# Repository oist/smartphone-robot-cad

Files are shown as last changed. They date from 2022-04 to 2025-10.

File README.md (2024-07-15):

# CAD for the OIST smartphone robots

This repository contains the CAD files for the OIST smartphone robots.

- [./body](./body) contains standard 3D CAD files used for the robot's 3D printed body.
- [./pcb](./pcb) contains the KiCad files for the robot's PCB and schematic design.

These two subprojects (body and pcb) have direct dependencies on each other as the 3D CAD design is based on the PCB design.
It is likely a good idea to manage the development of each on a separate branch and merge them together when necessary.

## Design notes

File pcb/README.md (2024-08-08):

# Smartphone Robot PCB and Schematic Design
The schematic and PCB design for the smartphone robot was done in KiCAD.

The most recent version was created in Kicad v7 so be sure to use that when opening the project else you may run into compatibility issues.

# Cloning the Repo
Currently this repo is an OIST internal repo, so read access is only given to specific users. Add external users for collaboration.

Note this repo uses a central library management system. Symbols, footprints, and models are maintained on a personal fork of the central kicad library repos. These forks are maintained as submodules within the kicad-symbols, kicad-footprints, and kicad-packages3D respectively under:

[https://github.com/oist/smartphone-robot-cad/tree/main/kicad/](https://github.com/oist/smartphone-robot-cad/tree/main/kicad/)

Those forks should all be public and you should be able to clone the main repo with submodules without additional access, but just in case, here are the links to the forks:
- [https://gitlab.com/topherbuckley/kicad-symbols](https://gitlab.com/topherbuckley/kicad-symbols)
- [https://gitlab.com/topherbuckley/kicad-footprints](https://gitlab.com/topherbuckley/kicad-footprints)
- [https://gitlab.com/topherbuckley/kicad-packages3D](https://gitlab.com/topherbuckley/kicad-packages3D)

The easiest way to clone including all submodules would likely be `git clone --recurse-submodules -j8 git@github.com:oist/smartphone-robot-cad.git' if you are having trouble with that, you can refer to these links for details:

- [StackOverflow](https://stackoverflow.com/questions/3796927/how-do-i-git-clone-a-repo-including-its-submodules)
- [Git Docs](https://git-scm.com/docs/git-submodule)

Note that because of the main repo and submodules are hosted on two different platforms (github and gitlab) you must have credentials for both platforms. You can use your github credentials to setup a gitlab account and add your existing SSH keys to your gitlab account. More on how to do that [here](https://docs.gitlab.com/ee/user/ssh.html)

# Setting up the Environment

KiCAD makes use of user configuration files to define libraries, so without modifying your setup, you will unlikely be able to resolve the majority of libraries used in this project. There are many ways to go about this, of which you can find more details in the links below:

- [Project Collaboration Tips](https://forum.kicad.info/t/project-and-libary-setup-for-sharing-and-collaboration-kicad-version-5/20842/2) (See section Simplify First Time Setup...)

This repo has been set up to make using environmental variables the easiest option. In the `config` directory you will find a subdirectories corresponding to minor version of KiCAD. If you add an environment variable for KICAD_CONFIG_HOME pointing to this `config` directory, KiCAD will use these configuration files rather than the defaults. On Ubuntu 20.04 the default is `~/.config/kicad/`. Note you must then open kicad from a terminal that as properly sourced the newly created environmental variables. In a bash terminal this would be:

```
source KICAD_CONFIG_HOME=[path_to_repo]/config
kicad
```

Note this will use blank (default or empty)  configurations, so feel free to copy/paste your personal configurations into this `config` directory as all files other than `sym-lib-table` and `fp-lib-table` are ignored by the `.gitignore` file.

# LED Inidications
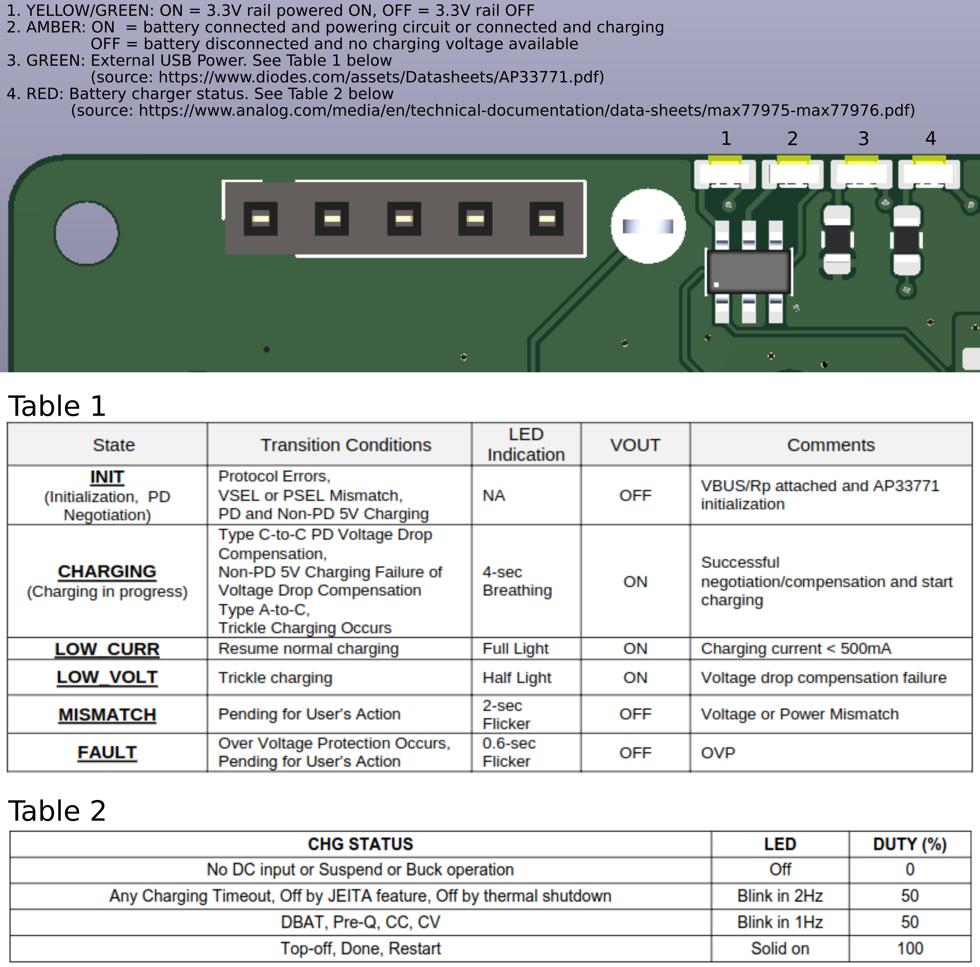
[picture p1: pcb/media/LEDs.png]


# Additional References
- [Good discussion on KiCAD Collaboration and Versioning](https://forum.kicad.info/t/working-collaborately-on-projects-using-git/16114/11)
- [Nice tools for versioning](https://jnavila.github.io/plotkicadsch/)

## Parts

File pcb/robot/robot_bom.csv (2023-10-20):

Manufacturer | Part Number | Ref | Qty Single Board | Description | Batch Size | Qty Total Batch | Customer Stock | Value | Footprint
Murata | GRM188R61A226ME15D | C1,C33,C34,C76,C78,C87,C93 | 7 | Unpolarized capacitor | 5 | 35 | 0 | 22uF | robot:C_0603_1608Metric
Murata | GRM1555C1H270JA01J | C2,C3,C18,C19,C45,C46 | 6 | Unpolarized capacitor | 5 | 30 | 0 | 27pF | robot:C_0402_1005Metric
Murata | GRM155R61E105KA12D | C4,C8,C10,C21,C22,C29,C47,C48,C50,C51,C52,C53,C54,C55,C69,C88,C94,C95,C105,C126 | 20 | Unpolarized capacitor | 5 | 100 | 10 | 1uF | robot:C_0402_1005Metric
Murata | GRM155R62A104KE14D | C5,C6,C7,C9,C11,C12,C13,C14,C15,C16,C24,C32,C35,C36,C37,C38,C39,C40,C41,C44,C57,C58,C59,C60,C61,C62,C63,C64,C65,C66,C70,C71,C72,C73,C85,C92,C102,C103,C104,C113,C114,C116,C119,C121 | 44 | Unpolarized capacitor | 5 | 220 | 0 | 0.1uF | robot:C_0402_1005Metric
Murata | GRM188R61E106KA73J | C17,C20,C25,C27,C42,C43,C67,C68,C75,C77,C80,C129,C130,C132,C134,C136 | 16 | Unpolarized capacitor | 5 | 80 | 0 | 10uF | robot:C_0603_1608Metric
Murata | GRM188R61E475KE11D | C23,C97,C100,C101,C124 | 5 | Unpolarized capacitor | 5 | 25 | 0 | 4.7uF | robot:C_0603_1608Metric
Samsung | CL10B474KO8NNNC | C26,C56 | 2 | Unpolarized capacitor | 5 | 10 | 0 | 0.47uF | robot:C_0603_1608Metric
Samsung | CL10A225KP8NNNC | C28,C49 | 2 | Unpolarized capacitor | 5 | 10 | 0 | 2.2uF | robot:C_0603_1608Metric
Samsung | CL10B224KA8NNNC | C30,C31 | 2 | Unpolarized capacitor | 5 | 10 | 0 | 0.22uF | robot:C_0603_1608Metric
Samsung Electro-Mechanics | CL21A476MRYNNNE | C81 | 1 | Unpolarized capacitor | 5 | 5 | 0 | 47uF | robot:C_0805_2012Metric
Murata | GRM31CD80J107MEA8K | C82,C83,C109,C125,C127 | 5 | Unpolarized capacitor | 5 | 25 | 20 | 100uF | robot:C_1206_3216Metric
Würth Elektronik | 885012205067 | C84,C115,C118 | 3 | Unpolarized capacitor | 5 | 15 | 0 | 10nF | robot:C_0402_1005Metric
Murata | GRM155R71H223KA12J | C110,C117,C120 | 3 | Unpolarized capacitor | 5 | 15 | 0 | 22nF | robot:C_0402_1005Metric
Murata | GCM155R71H152KA37D | C111 | 1 | Unpolarized capacitor | 5 | 5 | 0 | 1.5nF | robot:C_0402_1005Metric
Murata | GCM155R71H332KA37J | C112,C122 | 2 | Unpolarized capacitor | 5 | 10 | 0 | 3.3nF | robot:C_0402_1005Metric
Murata | GRM155R71H473KE14D | C123,C128 | 2 | Unpolarized capacitor | 5 | 10 | 0 | 47nF | robot:C_0402_1005Metric
Cal-Chip Electronics, Inc. | GMC32X5R107M16NT | C131,C137 | 2 | Unpolarized capacitor | 5 | 10 | 0 | 100uF | robot:C_1210_3225Metric
Harvatek Corporation | B12H1USD-20D000234U1930 | D1 | 1 | Light emitting diode | 5 | 5 | 0 | LED-RED | robot:B12H1UYG-20D000134U1930
Harvatek Corporation | B12H1UYG-20D000134U1930 | D2 | 1 | Light emitting diode | 5 | 5 | 0 | LED-YG | robot:B12H1UYG-20D000134U1930
Harvatek Corporation | B12H1UY--20D000134U1930 | D3 | 1 | Light emitting diode | 5 | 5 | 0 | LED-Amber | robot:B12H1UYG-20D000134U1930
Littelfuse Inc. | SMF13A | D4,D6,D10 | 3 | Zener diode | 5 | 15 | 0 | SMF13A | robot:D_SOD-123F
Harvatek Corporation | B12H1NG--20D000134U1930 | D5 | 1 | Light emitting diode | 5 | 5 | 0 | LED-GREEN | robot:B12H1UYG-20D000134U1930
KYOCERA AVX | SD2114S040S8R0 | D7 | 1 |  | 5 | 5 | 0 | D_Schottky | robot:SD2114S040S8R0
Diodes Incorporated | 1N4448HLP-7 | D9,D11 | 2 | Diode | 5 | 10 | 0 | IN4448HLP | robot:D_0402_1005Metric
Texas Instruments | TPS22998RYZR | IC1 | 1 | Power Switch ICs - Power Distribution | 5 | 5 | 0 | TPS22998RYZR | robot:TPS22998RYZR
Amphenol Commercial Products | 12401610E4#2A | J1 | 1 |  | 5 | 5 | 0 | USBC_Receptacle_SMD_RA | robot:CON_USB3.1-C_RCPT_SMD_RA_ACP_12401610E4#2A
Adam Tech | PH1-05-UA | J2 | 1 | Generic connector, single row, 01x05, script generated (kicad-library-utils/schlib/autogen/connector/) | 5 | 5 | 0 | Conn_01x05 | robot:PinSocket_1x05_P2.54mm_Vertical
JST | B6B-ZR-SM4-TF | J3,J5 | 2 | Generic connectable mounting pin connector, single row, 01x06, script generated (kicad-library-utils/schlib/autogen/connector/) | 5 | 10 | 0 | Conn_01x06_MountingPin | robot:CONN_B6B-ZR-SM4-TF_JST
GCT | USB4151-GF-C | J4 | 1 |  | 5 | 5 | 0 | USB4151-GF-C | robot:GCT_USB4151-GF-C_REVA
TAIYO YUDEN | NRS6028T1R5NMGJ | L1,L3 | 2 | Inductor | 5 | 10 | 0 | 1.5uH | robot:NRS6028T1R5NMGJ
Vishay | IHLP2020BZERR47M01 | L2,L4 | 2 | Inductor symbol for simulation only | 5 | 10 | 0 | 0.47uH | robot:Vishay-IHLP-2020BZ-FP_1.905x2.79-3D_2.0-0-0-MFG
ANBON SEMICONDUCTOR (INT'L) LIMITED | BSS138 | Q1,Q7 | 2 | N-MOSFET transistor, gate/source/drain | 5 | 10 | 0 | Q_NMOS_GDS | robot:SOT-23
ON Semiconductor | EFC8811R-TF | Q2 | 1 | EFC8811R-TF | 5 | 5 | 19 | EFC8811R-TF | robot:ON_Semiconductor-568AL-10_2013-O-MFG
ANBON SEMICONDUCTOR (INT'L) LIMITED | AS2312 | Q3 | 1 | 20V Vds, 0.63 Id, N-Channel MOSFET with ESD protection, SOT-523 | 5 | 5 | 0 | AS2312 | robot:SOT-23
Yangjie Electronic Technology | YJL3416A | Q4 | 1 | 20V Vds, 0.63 Id, N-Channel MOSFET with ESD protection, SOT-523 | 5 | 5 | 0 | YJL3416A | robot:SOT-23
Texas Instruments | SN74AHC125RGYR | Q5,Q6 | 2 | Buffer/Line Driver 4-CH Non-Inverting 3-ST CMOS 14-Pin VQFN EP T/R | 5 | 10 | 39 | SN74AHC125RGYR | robot:SN74AHC125RGYR
Walsin Technologies | WR04X102 JTL | R1,R5,R46,R47,R50 | 5 | Resistor | 5 | 25 | 0 | 1k | robot:R_0402_1005Metric
Stackpole Electronics | RMCF0402JT27R0 | R3,R4 | 2 | Resistor | 5 | 10 | 0 | 27 | robot:R_0402_1005Metric
Yageo | RC0402FR-1310RL | R6,R7,R32,R33,R41,R42 | 6 | Resistor | 5 | 30 | 0 | 10 | robot:R_0402_1005Metric
Stackpole Electronics | RMCF0603JT47K0 | R8,R18 | 2 | Resistor | 5 | 10 | 0 | 47K | robot:R_0603_1608Metric
Stackpole Electronics | RMCF0402FT80K6 | R9 | 1 | Resistor | 5 | 5 | 0 | 80.6k | robot:R_0402_1005Metric
Stackpole Electronics | RMCF0805ZT0R00 | R11,R52,R54,R67,R68,R69,R70,R71,R72,R73,R74,R77,R78 | 13 | Resistor | 5 | 65 | 0 | 0 | robot:R_0805_2012Metric
Walsin Technology | WR06X1003FTL | R12,R17,R49,R59,R60,R61,R89,R99 | 8 | Resistor | 5 | 40 | 0 | 100k | robot:R_0603_1608Metric
Stackpole Electronics | RMCF0603JT2K20 | R14,R15,R20,R21,R34,R35 | 6 | Resistor | 5 | 30 | 0 | 2.2k | robot:R_0603_1608Metric
Stackpole Electronics | RMCF0603JT510K | R16 | 1 | Resistor | 5 | 5 | 0 | 510k | robot:R_0603_1608Metric
Stackpole Electronics | RMCF0603JT200K | R19,R36 | 2 | Resistor | 5 | 10 | 0 | 200k | robot:R_0603_1608Metric
Stackpole Electronics | RMCF0603JT100R | R22,R23,R24,R25,R56,R58,R97 | 7 | Resistor | 5 | 35 | 0 | 100 | robot:R_0603_1608Metric
Walsin Technology | WR06X1002FTL | R28,R31,R96,R102 | 4 | Resistor | 5 | 20 | 0 | 10k | robot:R_0603_1608Metric
Panasonic | ERJ-3RQJR39V | R29,R30 | 2 | Resistor | 5 | 10 | 10 | 0.39 | robot:R_0603_1608Metric
Panasonic | ERJ-3EKF6493V | R37,R39 | 2 | Resistor | 5 | 10 | 0 | 649k | robot:R_0603_1608Metric
Stackpole Electronics | RMCF0603JT120K | R38,R40 | 2 | Resistor | 5 | 10 | 0 | 120k | robot:R_0603_1608Metric
Panasonic | ERJ-PA3J201V | R43,R45,R103,R104 | 4 | Resistor | 5 | 20 | 0 | 200 | robot:R_0603_1608Metric
Yageo | PA0805FRF470R005L | R44 | 1 | Resistor | 5 | 5 | 0 | 5m | robot:R_0805_2012Metric
Stackpole Electronics | RMCF0603FT2K00 | R48 | 1 | Resistor | 5 | 5 | 0 | 2k | robot:R_0603_1608Metric
Panasonic | ERJ-8CWJR010V | R51 | 1 | Resistor | 5 | 5 | 0 | 10m | robot:R_1206_3216Metric
Stackpole Electronics | RMCF0603FT113K | R53 | 1 | Resistor | 5 | 5 | 0 | 113K | robot:R_0603_1608Metric
Stackpole Electronics | RMCF0603FT14K0 | R55 | 1 | Resistor | 5 | 5 | 0 | 14k | robot:R_0603_1608Metric
Stackpole Electronics | RMCF0603ZT0R00 | R57,R75,R76,R79,R82,R83,R84,R85,R86,R87,R88,R90,R91,R92,R93,R94 | 16 | Resistor | 5 | 80 | 15 | 0 | robot:R_0603_1608Metric
Stackpole Electronics | RMCF0603FT16K0 | R62 | 1 | Resistor | 5 | 5 | 100 | 16k | robot:R_0603_1608Metric
Stackpole Electronics | RMCF0603JT5K10 | R63,R64 | 2 | Resistor | 5 | 10 | 0 | 5.1k | robot:R_0603_1608Metric
Yageo | AC0603JR-0710ML | R65 | 1 | Resistor | 5 | 5 | 0 | 10M | robot:R_0603_1608Metric
Stackpole Electronics | RMCF0603ZT0R00 | R95 | 1 | Resistor | 5 | 5 | 0 | 0 | robot:R_0603_1608Metric_3pin_Switch
YAGEO | RC0402FR-13150KL | R98 | 1 | Resistor | 5 | 5 | 0 | 150k | robot:R_0402_1005Metric
YAGEO | RC0402FR-07220KL | R100 | 1 | Resistor | 5 | 5 | 0 | 220k | robot:R_0402_1005Metric
YAGEO | RC0402FR-136K8L | R101 | 1 | Resistor | 5 | 5 | 0 | 6.8k | robot:R_0402_1005Metric
C&K | PTS815 SJM 250 SMTR LFS | S2 | 1 | E-SWITCH - TL3305AF260QG - TACTILE SW, SPST, 0.05A, 12VDC, SOLDER | 5 | 5 | 0 | PTS815 SJM 250 SMTR LFS | robot:SW4_PTS815 SJM 250 SMTR LFS_CNK
C&K | JS202011JCQN | S3,S4 | 2 | SWITCH SLIDE DPDT 300MA 6V | 5 | 10 | 0 | JS202011JCQN | robot:SW_JS202011JCQN
Molex | 0533980271 | SW1 | 1 | Single Pole Single Throw (SPST) switch | 5 | 5 | 0 | SW_SPST | robot:MOLEX_picoblade_SMT_2pin
Murata | NCU15WF104J6SRC | TH2 | 1 | Temperature dependent resistor | 5 | 5 | 0 | 100k | robot:R_0402_1005Metric
KOA Speer Electronics, Inc. | RCUCTE | TP1,TP2,TP3,TP4,TP5,TP6,TP7,TP8,TP9,TP10,TP11,TP13,TP14,TP15,TP16,TP17,TP18,TP19,TP20,TP21,TP22,TP23,TP24,TP26,TP27,TP33 | 26 | test point | 5 | 130 | 0 | SMD_0603 | robot:TestPoint_SMD_0603
Keystone Electronics | 5002 | TP30,TP34,TP39,TP40,TP41,TP42,TP43 | 7 | test point | 5 | 35 | 0 | TestPoint | robot:KEYSTONE_5002
STMicroelectronics | STWLC38JRM | U1 | 1 | Qi-compliant inductive wireless power receiver for 15W applications | 5 | 5 | 0 | STWLC38JRM | robot:BGA40C40P5X8_213X333X57
Winbond | W25Q128JVSIQ | U2 | 1 | 128Mb Serial Flash Memory, Standard/Dual/Quad SPI, SOIC-8 | 5 | 5 | 0 | W25Q128JVS | robot:SOIC-8_5.23x5.23mm_P1.27mm
Raspberry Pi | SC0914(13) | U3 | 1 |  | 5 | 5 | 0 | RP2040 | robot:RP2040-QFN-56
onsemi | NCP3901FCCT1G | U4 | 1 |  | 5 | 5 | 19 | NCP3901 | robot:NCP3901
Texas Instruments | LSF0102DCTR | U5 | 1 | Dual bidirectional multi-voltage level translator | 5 | 5 | 19 | LSF0102DCTR | robot:SOP65P400X130-8N
Maxim | MAX77857BEWB+ | U6 | 1 |  | 5 | 5 | 19 | MAX77857BEWB+ | robot:WLP-35_7x5_2.828x2.028mm
Diodes Inc. | AP2502KTR-G1 | U7 | 1 |  | 5 | 5 | 0 | AP2502KTR-G1 | robot:SOT95P280X145-6N
Texas Instruments | DRV8830DRCR | U8,U9 | 2 | DC Motor Driver I2C Control | 5 | 10 | 44 | DRV8830DRCR | robot:IC_DRV8830DRCR
Maxim | MAX77958EWV+T | U11 | 1 | USB-PD Controller | 5 | 5 | 19 | MAX77958EWV+T | robot:MAX77958EWV&plus_T
Texas Instruments | BQ27742YZFR-G1 | U12 | 1 | BQ27742YZFR-G1 | 5 | 5 | 19 | BQ27742YZFR-G1 | robot:Texas_Instruments-YZF0015-0-0-MFG
Maxim | MAX77976EFD+ | U13 | 1 |  | 5 | 5 | 19 | MAX77976EFD+ | robot:MAX77976
Maxim | MAX77642ANA+ | U14 | 1 | MAX77642ANA+ | 5 | 5 | 19 | MAX77642ANA+ | robot:Maxim-N252B2-1-0-A-MFG
Texas Instruments | TPD1E05U06DPYR | U15,U19,U20,U21,U22,U23,U26,U27,U28,U29 | 10 |  | 5 | 50 | 0 | TPD1E05U06 | robot:TPD1E05U06DPYR
onsemi | fpf1048bucx | U16 | 1 |  | 5 | 5 | 0 | fpf1048bucx | robot:BGA6N50P3X2_146X96X62N
Texas Instruments | TPS61253AYFFT | U17 | 1 | TPS6125xA 3.8-MHz, 5-V / 4-A Boost in 1.2-mm x 1.3-mm WCSP | 5 | 5 | 0 | TPS61253AYFFT | robot:Texas_Instruments-YFF0009-BGA9C40P3X3_119X129X62
Diodes Inc. | AP33771DKZ-13 | U18 | 1 | Diodes Inc. ACDC Decoder W-QFN4040-24 T&R 3K | 5 | 5 | 19 | AP33771DKZ-13 | robot:AP33771DKZ13
Texas Instruments | TVS0500DRVR | U24,U25 | 2 | Flat-Clamp Surge Protection Device. 5Vrwm, WSON-6 | 5 | 10 | 0 | TVS0500DRV | robot:TVS0500DRVR
ECS Inc. | ECS-120-8-36-CKM-TR3 | Y1 | 1 | Two pin crystal | 5 | 5 | 0 | ECS-120-8-36-CKM-TR3 | robot:XTAL_ECS-120-8-36-CKM-TR3

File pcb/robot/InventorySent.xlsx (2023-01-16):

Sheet: Sheet1
Inventory |  |  | Client: | Okinawa Institute of Science and Technology
 |  |  | Vendor: | NextPCB
 |  |  | Order Numbers | P-E56182ASB2, T-E56182AB2
 |  |  | Date | Dec 19, 2022
Ref | Quantity | Price (JPY) | Extended Price (JPY) | Part Number | Description
U6 | 6 | ￥275.5 | ￥1653 | MAX77857 | Switching Voltage Regulators 2.5V to 16V Input, 7A Switching Current High Efficiency Buck-Boost Converter
U4 | 6 | ￥208.8 | ￥1252.8 | NCP3901 | Power Switch ICs - Power Distribution DUAL INPUT SINGLE OUTPUT
U13 | 6 | ￥406.0333643 | ￥2436.200186 | MAX77976EFD+ | Battery Charger Li-Ion/Li-Pol 1-Cell 5.5A 4.15V to 4.46V 23-Pin FC2QFN
U14 | 6 | ￥404.65698 | ￥2427.94188 | MAX77642ANA+ | Multi Function Power Management IC Buck Boost 1-LDO 3-Out 0.5V to 5.5V 25-Pin WLP
Q5,Q6 | 11 | ￥9.63469 | ￥105.98159 | SN74AHC125RGYR | Buffer/Line Driver 4-CH Non-Inverting 3-ST CMOS 14-Pin VQFN EP T/R
U5 | 6 | ￥26.85738657 | ￥161.1443194 | LSF0102DCTR | Voltage Level Translator 2-CH Bidirectional Automotive 8-Pin SSOP T/R
U8,U9 | 11 | ￥137.6384286 | ￥1514.022714 | DRV8830DRCR | 7-V, 1-A H-bridge motor driver with speed regulation and I2C control 10-VSON -40 to 85
U11 | 6 | ￥346.84884 | ￥2081.09304 | MAX77958EWV+T | Industry's Simplest Standalone USB Type-C and USB Power Delivery Controller
U12 | 6 | ￥165.1661143 | ￥990.9966857 | BQ27742YZFR-G1 | Single cell Li-ion battery fuel gauge with integrated protection | battery gas gauge 15-DSBGA -40 to 85
U18 | 6 | ￥165.1661143 | ￥990.9966857 | AP33771DKZ-13 | AP33771 Series 24 V USB Type C Power Delivery 3.0 Sink Controller - WQFN-24
Q2 | 6 | ￥20.09521057 | ￥120.5712634 | EFC8811R-TF | Power Field-Effect Transistor, 2-Element, N-Channel, Silicon, Metal-oxide Semiconductor FET
L1,L3 | 15 | ￥36.1 | ￥541.5 | NRS6028T1R5NMGJ | Power Inductors - SMD 6028 1.5uH 20.8mOhms +/-30%Tol 4200mA
R29,R30 | 15 | ￥9.1 | ￥136.5 | ERJ-3RQJR39V | Current Sense Resistors - SMD 0603 0.39ohm 5% Curr Sense AEC-Q200
J3 | 10 | ￥62.1 | ￥621 | 67996-412HLF | Headers & Wire Housings 12P DR UNSHRD HRD TIN OVER NI
R6,R7,R32,R33,R41,R42 | 35 | ￥3.6 | ￥126 | RC0402FR-1310RL | Thick Film Resistors - SMD 10 Ohms 62.5 mW 0402 1%
R44 | 10 | ￥38 | ￥380 | PA0805FRF470R005L | Current Sense Resistors - SMD 5mOhms 1/2W 100PPM/C 0805 AEC-Q200
TP1,TP2,TP3,TP4,TP5,TP6,TP9,TP10,TP11,TP13,TP14,TP15,TP16,TP17,TP18,TP19,TP20,TP21,TP22,TP23,TP24,TP25,TP26,TP29,TP30,TP31,TP32,TP33,TP34,TP36 | 165 | ￥29.7 | ￥4900.5 | 5002 | Circuit Board Hardware - PCB TEST POINT WHITE .040
C23,C97,C100,C101 | 25 | ￥6.1 | ￥152.5 | CL21A475KAQNNNG | Multilayer Ceramic Capacitors MLCC - SMD/SMT 4.7uF+/-10% 25V X5R 0805
C26,C56 | 15 | ￥3.8 | ￥57 | CL10B474KO8NNNC | Multilayer Ceramic Capacitors MLCC - SMD/SMT 470nF+/-10% 16V X7R 0603
C30,C31 | 15 | ￥3.2 | ￥48 | CL10B224KA8NNNC | Multilayer Ceramic Capacitors MLCC - SMD/SMT SAMSUNG
C2,C3,C18,C19,C45,C46 | 35 | ￥1.5 | ￥52.5 | GRM1555C1H270JA01J | Multilayer Ceramic Capacitors MLCC - SMD/SMT PLEASE SEE MURATA'S SUGGESTED ALTERNATE GRM0335C1H270JA01D
C1,C33,C34,C76,C78,C8 | 50 | ￥12.9 | ￥645 | GRM188R61A226ME15D | Multilayer Ceramic Capacitors MLCC - SMD/SMT 22UF 10V 20% 0603
L2,L4 | 15 | ￥142.7 | ￥2140.5 | IHLP2020CZER1R5M11 | Power Inductors - SMD 1.5uH 20%
U24,U25 | 11 | 82.9 | 912 | TVS0500DRVR | TVS DIODE 5VWM 9.5VC 6WSON
U7,U10,U15,U19,U20,U21,U22,U23,U26,U27 | 56 | 53.5 | 2996 | TPD1E05U06DPYR | TVS DIODE 5.5VWM 14VC 2X1SON
S1 | 6 | 83 | 498 | JS202011SCQN | SWITCH SLIDE DPDT 300MA 6V
U3 | 6 | 148 | 888 | SC0914(13) | RP2040TR13
R43,R45 | 11 | 1.5 | 17 | CR0402-JW-201GLF | RES SMD 200 OHM 5% 1/16W 0402
R65 | 10 | 3.1 | 31 | AC0603JR-0710ML | RES SMD 10M OHM 5% 1/10W 0603
R52 | 10 | 2.2 | 22 | RMCF0603FT768K | RES 768K OHM 1% 1/10W 0603
R37,R39 | 11 | 2.2 | 24 | RMCF0603FT649K | RES 649K OHM 1% 1/10W 0603
R16 | 10 | 1.9 | 19 | RMCF0603JT510K | RES 510K OHM 5% 1/10W 0603
R63,R64 | 11 | 1.9 | 21 | RMCF0603JT5K10 | RES 5.1K OHM 5% 1/10W 0603
R18 | 10 | 1.9 | 19 | RMCF0603JT47K0 | RES 47K OHM 5% 1/10W 0603
R62 | 10 | 2.2 | 22 | RMCF0603FT45K3 | RES 45.3K OHM 1% 1/10W 0603
R57 | 10 | 1.9 | 19 | RMCF0603JT360R | RES 360 OHM 5% 1/10W 0603
R48 | 10 | 2.2 | 22 | RMCF0603FT2K00 | RES 2K OHM 1% 1/10W 0603
R54 | 10 | 2.2 | 22 | RMCF0603FT28K0 | RES 28K OHM 1% 1/10W 0603
R3,R4 | 11 | 1.5 | 17 | RMCF0402JT27R0 | RES 27 OHM 5% 1/16W 0402
R19,R36 | 11 | 1.9 | 21 | RMCF0603JT200K | RES 200K OHM 5% 1/10W 0603
R10,R11,R14,R15,R20,R21,R34,R35 | 100 | 0.81 | 81 | RMCF0603JT2K20 | RES 2.2K OHM 5% 1/10W 0603
R1,R5,R46,R47,R50 | 100 | 0.35 | 35 | WR04X102 JTL | RES 1K OHM 5% 1/16W 0402
R55 | 10 | 2.2 | 22 | RMCF0603FT14K0 | RES 14K OHM 1% 1/10W 0603
R38,R40 | 11 | 1.9 | 21 | RMCF0603JT120K | RES 120K OHM 5% 1/10W 0603
R53 | 10 | 2.2 | 22 | RMCF0603FT113K | RES 113K OHM 1% 1/10W 0603
R56 | 10 | 2.5 | 25 | RC0603JR-07110RL | RES 110 OHM 5% 1/10W 0603
R28,R31,R66 | 17 | 1.9 | 32 | RMCF0603JT10K0 | RES 10K OHM 5% 1/10W 0603
R17,R49,R59,R60,R61 | 28 | 1.9 | 53 | RMCF0603JG100K | RES 100K OHM 5% 1/10W 0603
R22,R23,R24,R25,R58 | 28 | 1.9 | 53 | RMCF0603JT100R | RES 100 OHM 5% 1/10W 0603
R51 | 6 | 78 | 468 | ERJ-8CWJR010V | RES 0.01 OHM 5% 1W 1206
Q3,Q4 | 11 | 33.4 | 367 | YJL3416A | N-CH MOSFET 20V 7A SOT-23-3L
Q1 | 6 | 22 | 132 | T2N7002AK,LM | MOSFET N-CH 60V 200MA SOT23
D6 | 10 | 6.8 | 68 | B1911UYG-20D000114U1930 | LED YELLOW GREEN CLEAR 1608 SMD
U16 | 6 | 121 | 726 | FPF1048BUCX | IC PWR SWITCH LOAD MGMT 6WLCSP
U2 | 6 | 260 | 1560 | W25Q128JVSIQ | IC FLASH 128MBIT SPI/QUAD 8SOIC
D7 | 6 | 111 | 666 | SD2114S040S8R0 | DIODE SCHOTTKY 40V 8A 2114
Y1 | 6 | 32 | 192 | ABLS-12.000MHZ-B4-T | CRYSTAL 12.0000MHZ 18PF SMD
J4 | 6 | 136 | 816 | USB4120-03-C | CONN RCPT USB2.0 TYP C 24POS SMD
J1 | 6 | 241 | 1446 | 12401610E4#2A | CONN RCP USB3.1 TYPEC 24P SMD RA
JP13,JP14,JP15,JP16,JP17,JP18,JP19,JP20,JP21,JP22 | 56 | 5.58 | 312 | QPC02SXGN-RC | CONN JUMPER SHORTING .100" GOLD
JP10,JP11,JP12 | 17 | 18.3 | 311 | 22284030 | CONN HEADER VERT 3POS 2.54MM
TP27,TP35 | 11 | 5.5 | 61 | PH1-02-UA | CONN HEADER VERT 2POS 2.54MM
JP8,JP9 | 11 | 5.5 | 61 | PH1-02-UA | CONN HEADER VERT 2POS 2.54MM
JP1,JP2,JP3,JP4,JP5,JP6,JP7 | 39 | 5.5 | 215 | PH1-02-UA | CONN HEADER VERT 2POS 2.54MM
C28,C49 | 11 | 7.7 | 85 | CL10A225KP8NNNC | CAP CER 2.2UF 10V X5R 0603
C4,C8,C10,C21,C22,C29,C47,C48,C50,C51,C52,C53,C54,C55,C69,C88,C105 | 100 | 3.59 | 359 | GRM155R61E105KA12D | CAP CER 1UF 25V X5R 0402
C17,C20,C25,C27,C42,C43,C67,C68,C75,C77,C80 | 61 | 18.76 | 1144 | GRM188R61E106KA73J | CAP CER 10UF 25V X5R 0603
C84 | 10 | 2.2 | 22 | CL05B103KA5NNNC | CAP CER 10000PF 25V X7R 0402
C5,C6,C7,C9,C11,C12,C13,C14,C15,C16,C24,C32,C35,C36,C37,C38,C39,C40,C41,C44,C57,C58,C59,C60,C61,C62,C63,C64,C65,C66,C70,C71,C72,C73,C74,C85,C90,C92,C102,C103,C104 | 226 | 0.66 | 149 | CL05A104KA5NNNC | CAP CER 0.1UF 25V X5R 0402
D4 | 6 | 15 | 90 | B0211NB--02D000114U1930 | 0.65(L)X0.38(W)X0.36(H) MM
U17 | 25 | 159.37 | 3984 | TPS61253AYFFT | TPS6125xA 3.8-MHz, 5-V / 4-A Boost in 1.2-mm x 1.3-mm WCSP
Total |  |  | ￥38699.74836

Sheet: header
Inventory |  |  | Client: | Okinawa Institute of Science and Technology
 |  |  | Vendor: | NextPCB
 |  |  | Order Numbers | P-E56182ASB2, T-E56182AB2
 |  |  | Date | Dec 19, 2022
Ref | Quantity | Price (JPY) | Extended Price (JPY) | Part Number | Description

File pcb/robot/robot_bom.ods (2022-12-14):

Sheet: robot_bom
Ref | Qty Single Board | Batch Size | Qty Total Batch | Stock | Spares | Total+Spares | Need to Buy | Value | Manufacturer | Part Number | Description | Footprint | Type
Q5,Q6 | 2 | 5 | 10 | 50 | 1 | 11 | 0 | SN74AHC125RGYR | Texas Instruments | SN74AHC125RGYR | Buffer/Line Driver 4-CH Non-Inverting 3-ST CMOS 14-Pin VQFN EP T/R | Ultra_Librarian:SN74AHC125RGYR
U8,U9 | 2 | 5 | 10 | 30 | 1 | 11 | 0 | DRV8830DRCR | Texas Instruments | DRV8830DRCR | DC Motor Driver I2C Control | Snapeda:IC_DRV8830DRCR
Q2 | 1 | 5 | 5 | 25 | 1 | 6 | 0 | EFC8811R-TF | ON Semiconductor | EFC8811R-TF | EFC8811R-TF | custom_transistors:ON_Semiconductor-568AL-10_2013-O-MFG
U4 | 1 | 5 | 5 | 25 | 1 | 6 | 0 | NCP3901 | onsemi | NCP3901 | Power Mux | custom_modules:NCP3901
U5 | 1 | 5 | 5 | 25 | 1 | 6 | 0 | LSF0102DCTR | Texas Instruments | LSF0102DCTR | Dual bidirectional multi-voltage level translator | Snapeda:SOP65P400X130-8N
U6 | 1 | 5 | 5 | 25 | 1 | 6 | 0 | MAX77857 | Maxim | MAX77857 | Switching Voltage Regulators 2.5V to 16V Input, 7A Switching Current High Efficiency Buck-Boost Converter | Package_BGA:WLP-35_7x5_2.828x2.028mm
U11 | 1 | 5 | 5 | 25 | 1 | 6 | 0 | MAX77958EWV+T | Maxim | MAX77958EWV+T | USB-PD Controller | Ultra_Librarian:MAX77958EWV&plus_T
U12 | 1 | 5 | 5 | 25 | 1 | 6 | 0 | BQ27742YZFR-G1 | Texas Instruments | BQ27742YZFR-G1 | BQ27742YZFR-G1 | Package_BGA:Texas_Instruments-YZF0015-0-0-MFG
U13 | 1 | 5 | 5 | 25 | 1 | 6 | 0 | MAX77976EFD+ | Maxim | MAX77976EFD+ |  | Ultra_Librarian:MAX77976
U14 | 1 | 5 | 5 | 25 | 1 | 6 | 0 | MAX77642ANA+ | Maxim | MAX77642ANA+ | MAX77642ANA+ | Package_BGA:Maxim-N252B2-1-0-A-MFG
U18 | 1 | 5 | 5 | 25 | 1 | 6 | 0 | AP33771DKZ-13 | Diodes Inc. | AP33771DKZ-13 | Diodes Inc. ACDC Decoder W-QFN4040-24 T&R 3K | Package_DFN_QFN:AP33771DKZ13
BT1 | 0 | 5 | 0 | 0 | 0 | 0 | 0 | DNP | Uxcell | a15042300ux0145 |  | custom_modules:battery26650_holderOnly
BT2 | 0 | 5 | 0 | 0 | 0 | 0 | 0 | DNP | Suprise Collection | 26650-5000-1 | Single-cell battery | custom_modules:battery26650
C1,C33,C34,C76,C78,C86,C87,C91,C93 | 9 | 5 | 45 | 0 | 5 | 50 | 45 | 22uF | Murata | GRM188R61A226ME15D | Unpolarized capacitor | Capacitor_SMD:C_0603_1608Metric
C2,C3,C18,C19,C45,C46 | 6 | 5 | 30 | 0 | 3 | 33 | 30 | 27pF | Murata | GRM1555C1H270JA01J | Unpolarized capacitor | Capacitor_SMD:C_0402_1005Metric
C4,C8,C10,C21,C22,C29,C47,C48,C50,C51,C52,C53,C54,C55,C69,C88,C105 | 17 | 5 | 85 | 0 | 9 | 94 | 85 | 1uF | Murata | GRM155R61E105KA12D | Unpolarized capacitor | Capacitor_SMD:C_0402_1005Metric
C5,C6,C7,C9,C11,C12,C13,C14,C15,C16,C24,C32,C35,C36,C37,C38,C39,C40,C41,C44,C57,C58,C59,C60,C61,C62,C63,C64,C65,C66,C70,C71,C72,C73,C74,C85,C90,C92,C102,C103,C104 | 41 | 5 | 205 | 0 | 21 | 226 | 205 | 0.1uF | Samsung | CL05A104KA5NNNC | Unpolarized capacitor | Capacitor_SMD:C_0402_1005Metric
C17,C20,C25,C27,C42,C43,C67,C68,C75,C77,C80 | 11 | 5 | 55 | 0 | 6 | 61 | 55 | 10uF | Murata | GRM188R61E106KA73J | Unpolarized capacitor | Capacitor_SMD:C_0603_1608Metric
C23,C97,C100,C101 | 4 | 5 | 20 | 0 | 2 | 22 | 20 | 4.7uF | Samsung | CL21A475KAQNNNG | Unpolarized capacitor | Capacitor_SMD:C_0805_2012Metric
C26,C56 | 2 | 5 | 10 | 0 | 1 | 11 | 10 | 0.47uF | Samsung | CL10B474KO8NNNC | Unpolarized capacitor | Capacitor_SMD:C_0603_1608Metric
C28,C49 | 2 | 5 | 10 | 0 | 1 | 11 | 10 | 2.2uF | Samsung | CL10A225KP8NNNC | Unpolarized capacitor | Capacitor_SMD:C_0603_1608Metric
C30,C31 | 2 | 5 | 10 | 0 | 1 | 11 | 10 | 0.22uF | Samsung | CL10B224KA8NNNC | Unpolarized capacitor | Capacitor_SMD:C_0603_1608Metric
C79 | 0 | 5 | 0 | 0 | 0 | 0 | 0 | DNP | DNP | DNP | Unpolarized capacitor | Capacitor_SMD:C_0805_2012Metric
C84 | 1 | 5 | 5 | 0 | 1 | 6 | 5 | 10nF | Samsung | CL05B103KA5NNNC | Unpolarized capacitor | Capacitor_SMD:C_0402_1005Metric
D4 | 1 | 5 | 5 | 0 | 1 | 6 | 5 | LED_B | Harvatek | B0211NB--02D000114U1930 | Light emitting diode | Diode_SMD:D_0603_1608Metric_Harvatek
D6 | 1 | 5 | 5 | 0 | 1 | 6 | 5 | LED_YG | Harvatek | B1911UYG-20D000114U1930 | Light emitting diode | Diode_SMD:D_0603_1608Metric_Harvatek
D7 | 1 | 5 | 5 | 0 | 1 | 6 | 5 | D_Schottky | KYOCERA AVX | SD2114S040S8R0 |  | Diode_SMD:SD2114S040S8R0
H1,H2,H3,H4 | 4 | 5 | 20 | 0 | 2 | 22 | 20 | MountingHole | N/A | N/A | Mounting Hole without connection | MountingHole:MountingHole_2.7mm_M2.5
J1 | 1 | 5 | 5 | 0 | 1 | 6 | 5 | USBC_Receptacle_SMD_RA | Amphenol Commercial Products | 12401610E4#2A |  | AltiumImports:CON_USB3.1-C_RCPT_SMD_RA_ACP_12401610E4#2A
J3 | 1 | 5 | 5 | 0 | 1 | 6 | 5 | 67996-412HLF | Amphenol ICC (FCI) | 67996-412HLF | CONN HEADER VERT 12POS 2.54MM | Connector_PinHeader_2.54mm:PinHeader_2x06_P2.54mm_Vertical
J4 | 1 | 5 | 5 | 0 | 1 | 6 | 5 | USB4120-03-C_REVA | GCT | USB4120-03-C |  | Connector_USB:GCT_USB4120-03-C_REVA
JP1,JP2,JP3,JP4,JP5,JP6,JP7 | 7 | 5 | 35 | 0 | 4 | 39 | 35 | Jumper_Bridged | Adam Tech | PH1-02-UA | Jumper, 2-pole, closed/bridged | custom_connectors:2.54mm_2pointJumperClosed
JP8,JP9 | 2 | 5 | 10 | 0 | 1 | 11 | 10 | Jumper_Open | Adam Tech | PH1-02-UA | Jumper, 2-pole, open | custom_connectors:2.54mm_2pointJumperOpen
JP10,JP11,JP12 | 3 | 5 | 15 | 0 | 2 | 17 | 15 | Jumper_3_Bridged12 | Molex | 22-28-4030 | Jumper, 3-pole, pins 1+2 closed/bridged | Connector_PinHeader_2.54mm:PinHeader_1x03_P2.54mm_Vertical_Pins12Connected
JP13,JP14,JP15,JP16,JP17,JP18,JP19,JP20,JP21,JP22 | 10 | 5 | 50 | 0 | 5 | 55 | 50 | Jumper | Sullins | QPC02SXGN-RC | Mechanical Jumper | custom_connectors:2.54mm_2pointJumper
L1,L3 | 2 | 5 | 10 | 0 | 1 | 11 | 10 | 1.5uH | TAIYO YUDEN | NRS6028T1R5NMGJ | Inductor | custom_inductors:NRS6028T1R5NMGJ
L2,L4 | 2 | 5 | 10 | 0 | 1 | 11 | 10 | 0.47uH | Vishay | IHLP2020BZERR47M01 | Inductor symbol for simulation only | custom_inductors:Vishay-IHLP-2020BZ-FP_1.905x2.79-3D_2.0-0-0-MFG
Q1 | 1 | 5 | 5 | 0 | 1 | 6 | 5 | Q_NMOS_GDS | Toshiba | T2N7002AK,LM | N-MOSFET transistor, gate/source/drain | Package_TO_SOT_SMD:SOT-23
Q3,Q4 | 2 | 5 | 10 | 0 | 1 | 11 | 10 | YJL3416A | Yangjie Electronic Technology | YJL3416A | 20V Vds, 0.63 Id, N-Channel MOSFET with ESD protection, SOT-523 | Package_TO_SOT_SMD:SOT-23
R1,R5,R46,R47,R50 | 5 | 5 | 25 | 0 | 3 | 28 | 25 | 1k | Walsin Technologies | WR04X102 JTL | Resistor | Resistor_SMD:R_0402_1005Metric
R3,R4 | 2 | 5 | 10 | 0 | 1 | 11 | 10 | 27 | Stackpole Electronics | RMCF0402JT27R0 | Resistor | Resistor_SMD:R_0402_1005Metric
R6,R7,R32,R33,R41,R42 | 6 | 5 | 30 | 0 | 3 | 33 | 30 | 10 | Yageo | RC0402FR-1310RL | Resistor | Resistor_SMD:R_0402_1005Metric
R10,R11,R14,R15,R20,R21,R34,R35 | 8 | 5 | 40 | 0 | 4 | 44 | 40 | 2.2k | Stackpole Electronics | RMCF0603JT2K20 | Resistor | Resistor_SMD:R_0603_1608Metric
R16 | 1 | 5 | 5 | 0 | 1 | 6 | 5 | 510k | Stackpole Electronics | RMCF0603JT510K | Resistor | Resistor_SMD:R_0603_1608Metric
R17,R49,R59,R60,R61 | 5 | 5 | 25 | 0 | 3 | 28 | 25 | 100k | Stackpole Electronics | RMCF0603JG100K | Resistor | Resistor_SMD:R_0603_1608Metric
R18 | 1 | 5 | 5 | 0 | 1 | 6 | 5 | 47K | Stackpole Electronics | RMCF0603JT47K0 | Resistor | Resistor_SMD:R_0603_1608Metric
R19,R36 | 2 | 5 | 10 | 0 | 1 | 11 | 10 | 200k | Stackpole Electronics | RMCF0603JT200K | Resistor | Resistor_SMD:R_0603_1608Metric
R22,R23,R24,R25,R58 | 5 | 5 | 25 | 0 | 3 | 28 | 25 | 100 | Stackpole Electronics | RMCF0603JT100R | Resistor | Resistor_SMD:R_0603_1608Metric
R28,R31,R66 | 3 | 5 | 15 | 0 | 2 | 17 | 15 | 10k | Stackpole Electronics | RMCF0603JT10K0 | Resistor | Resistor_SMD:R_0603_1608Metric
R29,R30 | 2 | 5 | 10 | 0 | 1 | 11 | 10 | 0.39 | Panasonic | ERJ-3RQJR39V | Resistor | Resistor_SMD:R_0603_1608Metric
R37,R39 | 2 | 5 | 10 | 0 | 1 | 11 | 10 | 649k | Stackpole Electronics | RMCF0603FT649K | Resistor | Resistor_SMD:R_0603_1608Metric
R38,R40 | 2 | 5 | 10 | 0 | 1 | 11 | 10 | 120k | Stackpole Electronics | RMCF0603JT120K | Resistor | Resistor_SMD:R_0603_1608Metric
R43,R45 | 2 | 5 | 10 | 0 | 1 | 11 | 10 | 200 | Bourns | CR0402-JW-201GLF | Resistor | Resistor_SMD:R_0603_1608Metric
R44 | 1 | 5 | 5 | 0 | 1 | 6 | 5 | 5m | Yageo | PA0805FRF470R005L | Resistor | Resistor_SMD:R_0805_2012Metric
R48 | 1 | 5 | 5 | 0 | 1 | 6 | 5 | 2k | Stackpole Electronics | RMCF0603FT2K00 | Resistor | Resistor_SMD:R_0603_1608Metric
R51 | 1 | 5 | 5 | 0 | 1 | 6 | 5 | 10m | Panasonic | ERJ-8CWJR010V | Resistor | Resistor_SMD:R_1206_3216Metric
R52 | 1 | 5 | 5 | 0 | 1 | 6 | 5 | 768k | Stackpole Electronics | RMCF0603FT768K | Resistor | Resistor_SMD:R_0603_1608Metric
R53 | 1 | 5 | 5 | 0 | 1 | 6 | 5 | 113K | Stackpole Electronics | RMCF0603FT113K | Resistor | Resistor_SMD:R_0603_1608Metric
R54 | 1 | 5 | 5 | 0 | 1 | 6 | 5 | 28k | Stackpole Electronics | RMCF0603FT28K0 | Resistor | Resistor_SMD:R_0603_1608Metric
R55 | 1 | 5 | 5 | 0 | 1 | 6 | 5 | 14k | Stackpole Electronics | RMCF0603FT14K0 | Resistor | Resistor_SMD:R_0603_1608Metric
R56 | 1 | 5 | 5 | 0 | 1 | 6 | 5 | 110 | Yageo | RC0603JR-07110RL | Resistor | Resistor_SMD:R_0603_1608Metric
R57 | 1 | 5 | 5 | 0 | 1 | 6 | 5 | 360 | Stackpole Electronics, Inc. | RMCF0603JT360R | Resistor | Resistor_SMD:R_0603_1608Metric
R62 | 1 | 5 | 5 | 0 | 1 | 6 | 5 | 45.3k | Stackpole Electronics | RMCF0603FT45K3 | Resistor | Resistor_SMD:R_0603_1608Metric
R63,R64 | 2 | 5 | 10 | 0 | 1 | 11 | 10 | 5.1k | Stackpole Electronics | RMCF0603JT5K10 | Resistor | Resistor_SMD:R_0603_1608Metric
R65 | 1 | 5 | 5 | 0 | 1 | 6 | 5 | 10M | Yageo | AC0603JR-0710ML | Resistor | Resistor_SMD:R_0603_1608Metric
S1 | 1 | 5 | 5 | 0 | 1 | 6 | 5 | JS202011SCQN | C&K | JS202011SCQN | SWITCH SLIDE DPDT 300MA 6V | Button_Switch_SMD:Switch_Slide_JS202011SCQN
TH1 | 0 | 5 | 0 | 0 | 0 | 0 | 0 | DNP | Semitec | 103AT-5-1P-FT | Temperature dependent resistor | custom_modules:battery26650_thermistor
TP1,TP2,TP3,TP4,TP5,TP6,TP9,TP10,TP11,TP13,TP14,TP15,TP16,TP17,TP18,TP19,TP20,TP21,TP22,TP23,TP24,TP25,TP26,TP29,TP30,TP31,TP32,TP33,TP34,TP36 | 30 | 5 | 150 | 0 | 15 | 165 | 150 | TP5002 | Keystone Electronics | 5002 | test point | TestPoint:KEYSTONE_5002
TP27,TP35 | 2 | 5 | 10 | 0 | 1 | 11 | 10 | 2PinHeader | Adam Tech | PH1-02-UA | Generic connector, single row, 01x02, script generated (kicad-library-utils/schlib/autogen/connector/) | Connector_PinHeader_2.54mm:PinHeader_1x02_P2.54mm_Vertical
U1 | 0 | 5 | 0 | 0 | 0 | 0 | 0 | DNP | TDK | WRM483265-10F5-12V-G |  | custom_modules:WRM483265-10F5-12V-G
U2 | 1 | 5 | 5 | 0 | 1 | 6 | 5 | W25Q128JVS | Winbond | W25Q128JVSIQ | 128Mb Serial Flash Memory, Standard/Dual/Quad SPI, SOIC-8 | Package_SO:SOIC-8_5.23x5.23mm_P1.27mm
U3 | 1 | 5 | 5 | 0 | 1 | 6 | 5 | RP2040 | Raspberry Pi | SC0914(13) |  | RP2040_minimal:RP2040-QFN-56
U7,U10,U15,U19,U20,U21,U22,U23,U26,U27 | 10 | 5 | 50 | 0 | 5 | 55 | 50 | TPD1E05U06 | Texas Instruments | TPD1E05U06DPYR |  | Package_X1SON:TPD1E05U06DPYR
U16 | 1 | 5 | 5 | 0 | 1 | 6 | 5 | fpf1048bucx | onsemi | fpf1048bucx |  | Package_BGA:BGA6N50P3X2_146X96X62N
U17 | 1 | 5 | 5 | 0 | 1 | 6 | 5 | TPS61253AYFFR | Texas Instruments | TPS61253AYFFR | TPS6125xA 3.8-MHz, 5-V / 4-A Boost in 1.2-mm x 1.3-mm WCSP | Package_BGA:Texas_Instruments-YFF0009-BGA9C40P3X3_119X129X62
U24,U25 | 2 | 5 | 10 | 0 | 1 | 11 | 10 | TVS0500DRV | Texas Instruments | TVS0500DRVR | Flat-Clamp Surge Protection Device. 5Vrwm, WSON-6 | Package_SON:TVS0500DRVR
Y1 | 1 | 5 | 5 | 0 | 1 | 6 | 5 | ABLS-12.000MHZ-B4-T | Abracon LLC | ABLS-12.000MHZ-B4-T | Two pin crystal | RP2040_minimal:Crystal_SMD_HC49-US

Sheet: labels
Ref | Q5,Q6 | Ref | U8,U9
MPN | SN74AHC125RGYR | MPN | DRV8830DRCR
Description | Buffer/Line Driver 4-CH Non-Inverting 3-ST CMOS 14-Pin VQFN EP T/R | Description | DC Motor Driver I2C Control
Qty | 11 | Qty | 11
Ref | Q2 | Ref | U4
MPN | EFC8811R-TF | MPN | NCP3901
Description | EFC8811R-TF | Description | Power Mux
Qty | 6 | Qty | 6
Ref | U5 | Ref | U6
MPN | LSF0102DCTR | MPN | MAX77857
Description | Dual bidirectional multi-voltage level translator | Description | Switching Voltage Regulators 2.5V to 16V Input, 7A Switching Current High Efficiency Buck-Boost Converter
Qty | 6 | Qty | 6
Ref | U11 | Ref | U12
MPN | MAX77958EWV+T | MPN | BQ27742YZFR-G1
Description | USB-PD Controller | Description | BQ27742YZFR-G1
Qty | 6 | Qty | 6
Ref | U13 | Ref | U14
MPN | MAX77976EFD+ | MPN | MAX77642ANA+
Description | 0 | Description | MAX77642ANA+
Qty | 6 | Qty | 6

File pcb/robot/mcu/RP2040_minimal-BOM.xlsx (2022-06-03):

RP2040_minimal_r1 BOM
Item | Quantity | Reference | Part | Voltage | Current | Power | Material | Size | Tolerance | Manufacturer | Manuf. Part # | Description | Notes
1 | 3 | C1,C4,C17 | 10u | 16V |  |  | X5R | 0805_2012Metric | 10% | Murata | GRM21BR61C106KE15K | CAP CER 10UF 16V X5R 0805 | Or equivalent
2 | 2 | C2, C3 | 27p | 50V |  |  | C0G | 0402_1005Metric | 5% | Murata | GCM1555C1H270JA16D | CAP CER 27PF 50V C0G/NP0 0402 | Or equivalent
3 | 10 | C5, C6, C7, C9, C11, C12, C13, C14, C15, C16 | 100n | 25V |  |  | X7R | 0402_1005Metric | 10% | Murata | GRM155R71E104KE14J | CAP CER 0.1UF 25V X7R 0402 | Or equivalent
4 | 2 | C8, C10 | 1u | 10V |  |  | X6S | 0402_1005Metric | 10% | Murata | GRM155C81A105KA12D | CAP CER 1UF 10V X6S 0402 | Or equivalent
5 | 1 | J1 | USB_B_Micro |  |  |  |  |  |  | Amphenol | 10103594-0001LF | CONN RCPT USB2.0 MICRO B SMD R/A | Or equivalent
6 | 1 | J2 | 1x2 way header |  |  |  |  |  |  | Samtec | TSW-102-23-T-S | 2.54mm pin header 1x2 | Or equivalent
7 | 2 | J3, J4 | 2x18 way header |  |  |  |  |  |  | Samtec | TSW-118-23-T-D | 2.54mm pin header 2x18 | Or equivalent
8 | 2 | R1, R5 | 1k |  |  | 63mW |  | 0402_1005Metric | 1% | Yageo | RC0402FR-071KP | RES SMD 1K OHM 1% 1/16W 0402 | Or equivalent
9 | 1 | R2 | DNF |  |  |  |  | 0402_1005Metric |  |  |  |  | Do Not Fit
10 | 2 | R3, R4 | 27.4 |  |  | 63mW |  | 0402_1005Metric | 1% | Yageo | RC0402FR-0727R4L | RES SMD 27.4 OHM 1% 1/16W 0402 | Or equivalent
11 | 1 | U1 | NCP1117-3.3 |  |  |  |  | SOT-223-3 |  | ON Semiconductor | NCP1117ST33T3G | IC REG LINEAR 3.3V 1A SOT223
12 | 1 | U2 | W25Q128JVS |  |  |  |  | SOIC-8 |  | Winbond | W25Q128JVSIQ TR | IC FLASH 128M SPI 133MHZ 8SOIC
13 | 1 | U3 | RP2040 |  |  |  |  | QFN56 |  | Raspberry Pi | RP2040
14 | 1 | Y1 | ABLS-12.000MHZ-B4-T |  |  |  |  | HC49-US |  | Abracon | ABLS-12.000MHZ-B4-T | CRYSTAL 12.0000MHZ 18PF SMD

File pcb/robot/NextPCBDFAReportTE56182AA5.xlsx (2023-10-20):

NEXTPCB DFA report
Project Number： |  | Prepared by: |  |  |  |  | Date: 20230904
Item | Problem description 问题描述 | Reference location 影响位置 | MPN 物料名称 | Impact 影响 | Image 图片 | NextPCB Suggestion 建议 | Customer feedback 客户反馈 | Severity 严重度 | Status 状态
1 | The space between the pad is large than the datasheet | U8;U9 | DRV8830DRCR | will cannot be soldered in the pads and easy to cause assembly problem |  | Please update the files to match with datasheet | Updated. Please verify. Note the gerber being compared is the solder paste layer rather than the mask and copper layers, which are all different. They should all match the datasheet’s specs See page 34 rather than the chip dimensions on page 32 that you referenced. | Middle | open
2 | There is not pin1 mark in the files | U4; | NCP3901FCCT1G | cannot ensure the Pin1 |  | Please add it in the silkscreen layer | Added a dot on the corner of the silkscreen layer. Please confirm that this is sufficient, or should be replaced by larger A1 text. | Middle | open
3 | The J4 is not match with datasheet | J4 | USB4120-03-C | couldn't be soldered in the board |  | Please update the files to match with datasheet | This was actually a mistake in the part number. This should have been part number USB4151-GF-C. The footprint should be correct for that. Please update our BOM quotation as well, as the correct part is a bit more expensive. Sorry for this error. | Middle | open
4 | There are three pads in the R95 | R95 | RMCF0603ZT0R00 | couldn't ensure which one should we soldered |  | Please help to mark | I added to the silkscreen to indicate which of the two to add the 0 ohm resistor over. The silkscreen is filled in this area. There is no silkscreen over one pad and this is the pad to remain unpopulated. Please let me know if this is unclear. | Middle | open

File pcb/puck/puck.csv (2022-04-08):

Reference | Quantity | Value | Footprint | Datasheet | Digi-Key Part Number | A1_MIN | A_MAX | A_MIN | A_NOM | B_MAX | B_MIN | B_NOM | D2_MAX | D_MAX | D_MIN | D_NOM | E1_MAX | E1_MIN | E1_NOM | E2_MAX | ENOM | E_MAX | E_MIN | E_NOM | L_MAX | L_MIN | L_NOM | MANUFACTURER | PARTREV | PIN_COUNT | STANDARD | MAXIMUM_PACKAGE_HEIGHT
C2 C1 C6 | 3 | C_1uF | Capacitor_SMD:C_0603_1608Metric | ~ | 1276-1102-1-ND
C3 C7 C4 | 3 | DNP | custom_passives:C_0603_1608Metric_DNP | ~
C5 | 1 | C_0.1uF | Capacitor_SMD:C_0603_1608Metric |  | 1276-1006-1-ND
D1 | 1 | 1N5819 | Diode_SMD:D_SOD-123 | http://www.vishay.com/docs/88525/1n5817.pdf | 1N5819HW-FDICT-ND
J1 | 1 | PicoBlade_5Pin_SMD_Horizontal | Connector_Molex:Molex_PicoBlade_53261-0571_1x05-1MP_P1.25mm_Horizontal | https://www.molex.com/pdm_docs/sd/532610571_sd.pdf | WM7623CT-ND
J2 | 1 | PicoBlade_2Pin_SMD_Horizontal | Connector_Molex:Molex_PicoBlade_53261-0271_1x02-1MP_P1.25mm_Horizontal | https://www.molex.com/pdm_docs/sd/532610271_sd.pdf | WM7620CT-ND
L1 | 1 | 10u | custom_inductors:IND_LQH43PN100M26L |  | 490-12780-1-ND |  |  |  |  |  |  |  |  |  |  |  |  |  |  |  |  |  |  |  |  |  |  | Murata | N/A |  | Manufacturer Recommendations | 2.8mm
Q1 Q2 | 2 | DMN3018SSD-13 | SOIC127P600X170-8N |  | DMN3018SSD-13DICT-ND | 0.1 | 1.7 | 1.7 | 1.7 | 0.5 | 0.3 | 0.4 | 0.0 | 4.95 | 4.85 | 4.9 | 3.9 | 3.8 | 3.85 | 0.0 | 1.27 | 6.1 | 5.9 | 6.0 | 0.82 | 0.62 | 0.72 | Diodes | 5-2 | 8.0 | IPC 7351B
Q3 | 1 | IRLR6225TRPBF | digikey-footprints:TO-252-3 | https://www.infineon.com/dgdl/irlr6225pbf.pdf?fileId=5546d462533600a40153566d99bc26c1 | IRLR6225TRPBFCT-ND
R1 | 1 | 63.4k | Resistor_SMD:R_0603_1608Metric | ~ | RMCF0603FT63K4CT-ND
R2 | 1 | 6.65k | Resistor_SMD:R_0603_1608Metric | ~ | RMCF0603FT6K65CT-ND
R3 | 1 | 69.8 | Resistor_SMD:R_0603_1608Metric | ~ | RMCF0603FT69K8CT-ND
R4 R5 | 2 | NetTie | custom_passives:R_0603_1608Metric_NetTie
TP3 TP5 TP2 TP6 TP1 TP7 TP4 | 7 | TestPoint_SMDpad | TestPoint:TestPoint_Pad_D2.0mm | ~
TP8 TP9 TP10 TP11 | 4 | TestPoint_CurrentShunt | custom_connectors:SAMTEC_TSM-102-01-T-SH | https://www.digikey.jp/product-detail/en/kycon-inc/SX1100-B/2092-SX1100-B-ND/9990206 | SAM10785-ND
U1 | 1 | AP3012KTR-G1 | custom_modules:SOT95P280X145-5N |  | AP3012KTR-G1DICT-ND |  |  |  |  |  |  |  |  |  |  |  |  |  |  |  |  |  |  |  |  |  |  | Diodes Inc. | 1.6 |  | IPC 7351B | 1.45 mm
U2 | 1 | SeeeduinoXIAO | custom_modules:Seeeduino_XIAO-MOUDLE14P-2p54-21X17p8MM | https://media.digikey.com/pdf/Data%20Sheets/Seeed%20Technology/102010328_Web.pdf | 1597-102010328-ND
U3 | 1 | INA250A3PWR | custom_modules:SOP65P640X120-16N | https://www.ti.com/lit/ds/symlink/ina250.pdf?ts=1615261358271 | 296-43803-1-ND

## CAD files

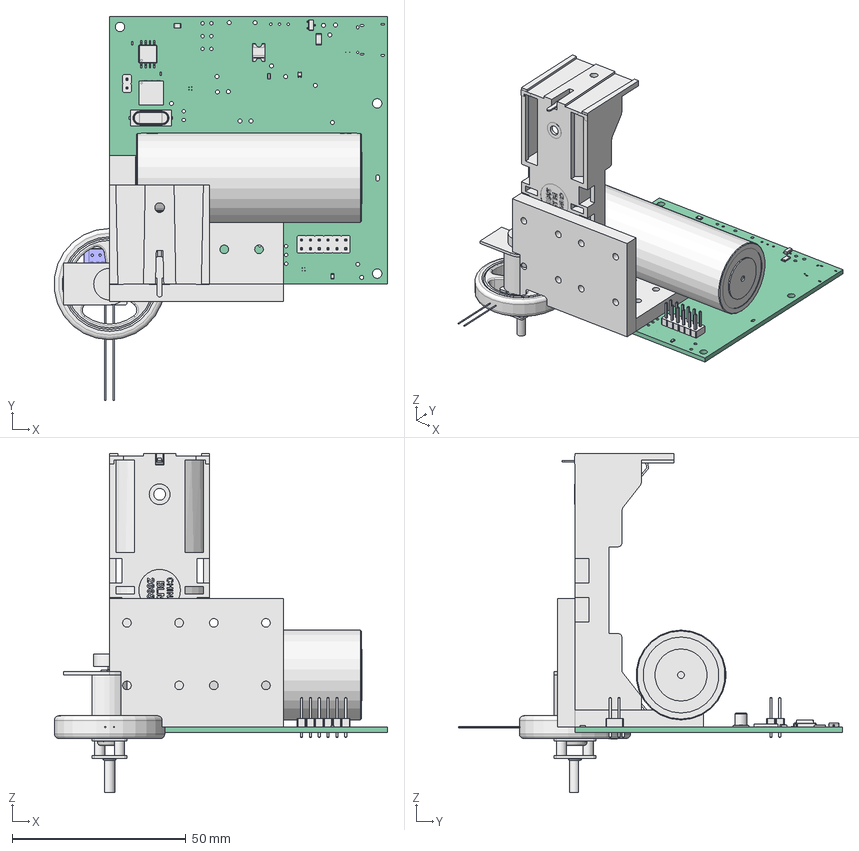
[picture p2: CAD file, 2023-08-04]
3DCAD/RobotAssembly3.0.FCStd
95.9 x 110.5 x 97.7 mm
BodyBracket
baseModel
New Marking
JST Logo
pcbMagnet
12401832E402A
BODY-SON
logo
logo001
logo002
logo003
logo004
logo005
logo006
logo007
ball array
ball array001
ball array002
ball array003
ball array004
ball array005
ball array006
ball array007
ball array008
ball array009
ball array010
ball array011
ball array012
ball array013
ball array014
ball array015
ball array016
ball array017
ball array018
ball array019
ball array020
ball array021
ball array022
ball array023
ball array024
ball array025
ball array026
ball array027
42f9e23d-407a-11ed-aca1-3708b1b5f0f2_part
42f9e23e-407a-11ed-aca1-3708b1b5f0f2_part
42f9e23e-407a-11ed-aca1-3708b1b5f0f2_part001
42f9e23e-407a-11ed-aca1-3708b1b5f0f2_part002
42f9e23e-407a-11ed-aca1-3708b1b5f0f2_part003
42f9e23e-407a-11ed-aca1-3708b1b5f0f2_part004
42f9e23e-407a-11ed-aca1-3708b1b5f0f2_part005
42f9e23e-407a-11ed-aca1-3708b1b5f0f2_part006
42f9e23e-407a-11ed-aca1-3708b1b5f0f2_part007
42f9e23e-407a-11ed-aca1-3708b1b5f0f2_part008
42f9e23e-407a-11ed-aca1-3708b1b5f0f2_part009
42f9e23e-407a-11ed-aca1-3708b1b5f0f2_part010
42f9e23e-407a-11ed-aca1-3708b1b5f0f2_part011
42f9e23e-407a-11ed-aca1-3708b1b5f0f2_part012
42f9e23e-407a-11ed-aca1-3708b1b5f0f2_part013
42f9e23e-407a-11ed-aca1-3708b1b5f0f2_part014
42f9e23e-407a-11ed-aca1-3708b1b5f0f2_part015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

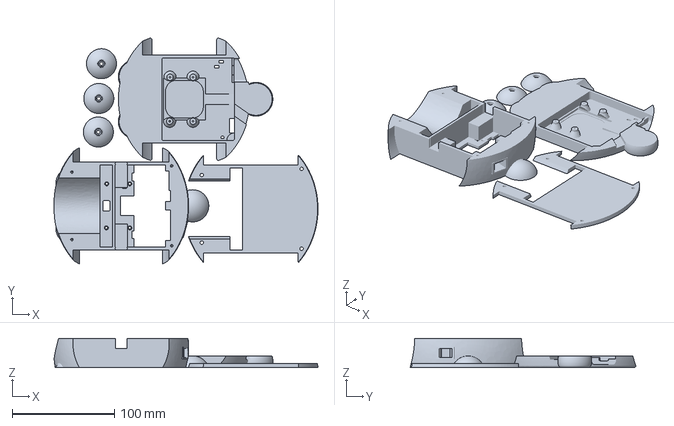
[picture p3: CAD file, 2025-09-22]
body/UMS5_body-Assembly.3mf
258.0 x 220.6 x 28.5 mm

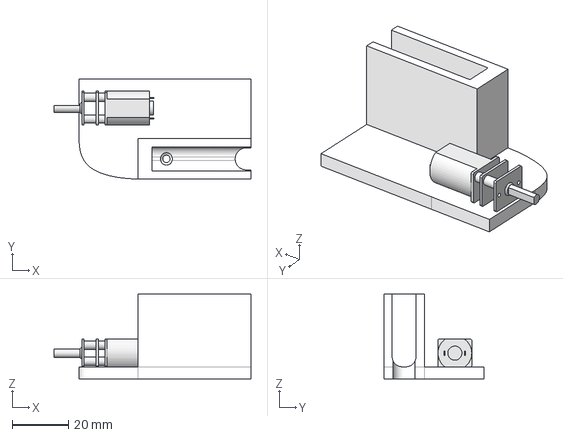
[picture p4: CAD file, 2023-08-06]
3DCAD/pixel3a_mount.FCStd
69.9 x 35.5 x 30.0 mm
mount
gearedMotor

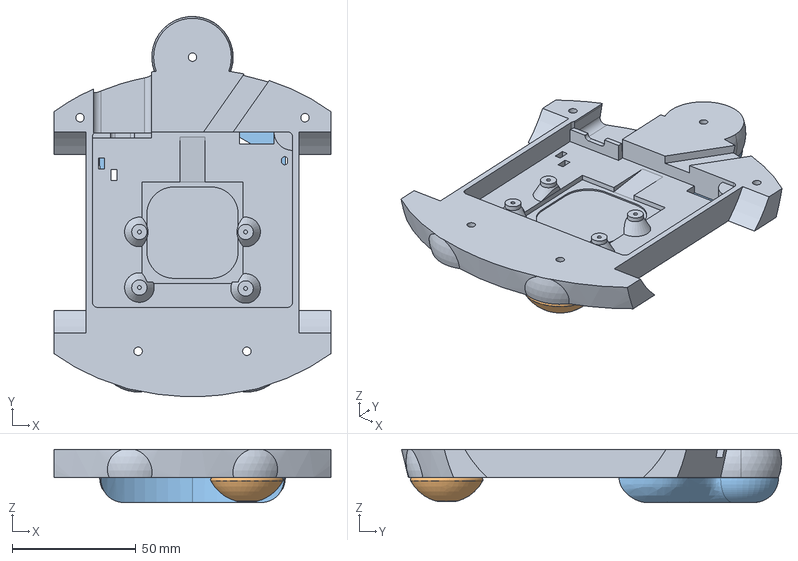
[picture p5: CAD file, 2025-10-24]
body/body.FCStd
112.0 x 153.8 x 21.5 mm
bottom
foot
puckCatchingTail

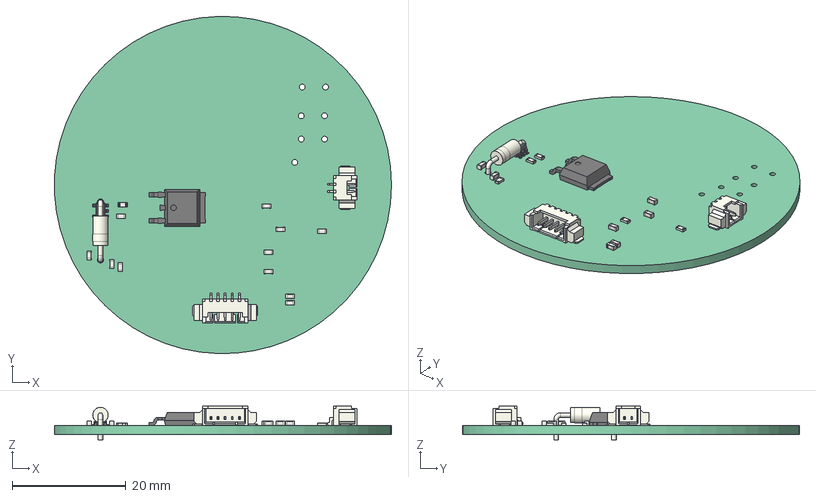
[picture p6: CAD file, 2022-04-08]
pcb/puck/puck_pcb.FCStd
59.2 x 59.2 x 5.90 mm
Pcb_f239
J2_Molex_53261_0271_606AF72E
J1_Molex_53261_0571_60808297
R3_R_0603_1608Metric_608088A1
R2_R_0603_1608Metric_60808871
R1_R_0603_1608Metric_60808787
D1_D_DO-41_SOD81_P10.16mm_Horizontal_608087F2
C2_C_0603_1608Metric_608087BA
C1_C_0603_1608Metric_60808757
R5_R_0603_1608Metric_606C0BF9
R4_R_0603_1608Metric_606C0D03
C7_C_0603_1608Metric_606C0BC8
C6_C_0603_1608Metric_606C0C6D
C5_C_0603_1608Metric_6087A65F
C4_C_0603_1608Metric_6089D4F3
C3_C_0603_1608Metric_6084614A
Q3_TO_252_2_6067AF53
U1_SOT_23_5_60808839

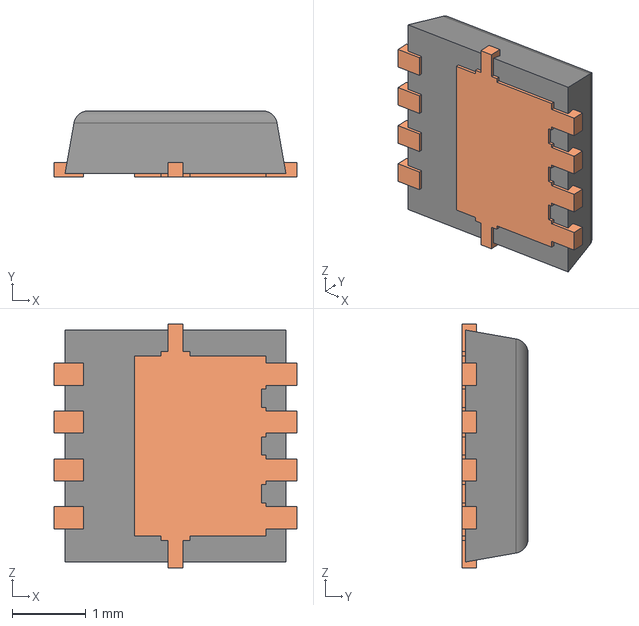
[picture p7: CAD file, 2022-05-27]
pcb/robot/ALTIUM_EMBEDDED_MODELS/DNH0008A.stp
3.30 x 0.9 x 3.31 mm

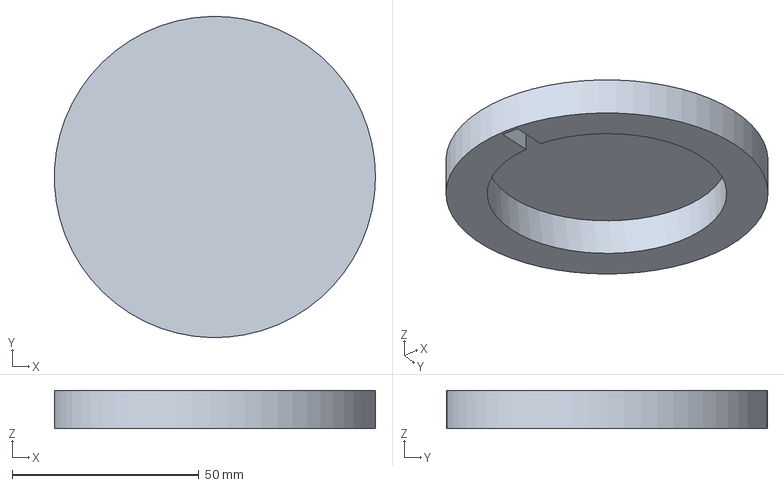
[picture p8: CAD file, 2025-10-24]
body/puck.FCStd
85.9 x 86.0 x 10.2 mm

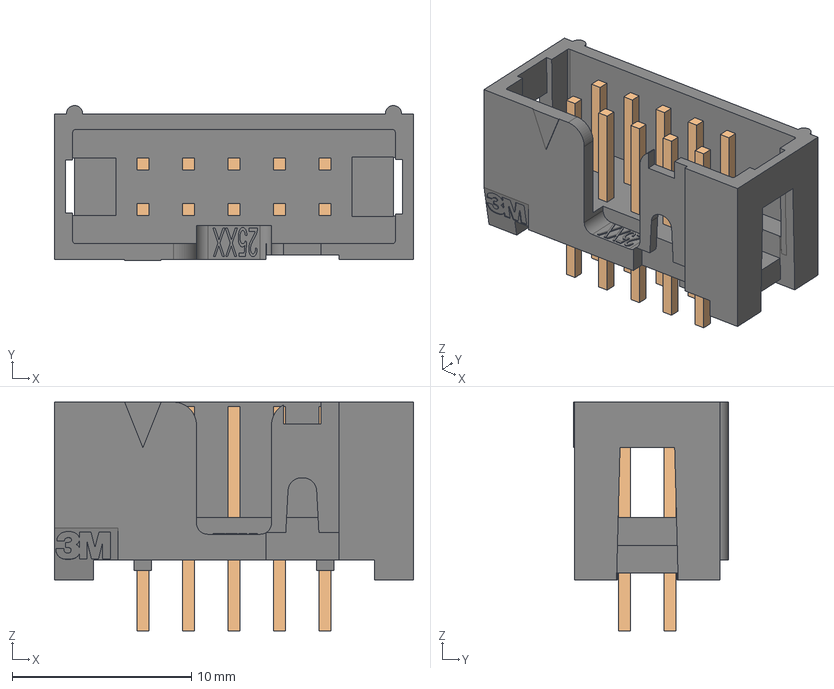
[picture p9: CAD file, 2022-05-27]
pcb/robot/ALTIUM_EMBEDDED_MODELS/3M_2510-6002.stp
20.0 x 8.64 x 12.8 mm

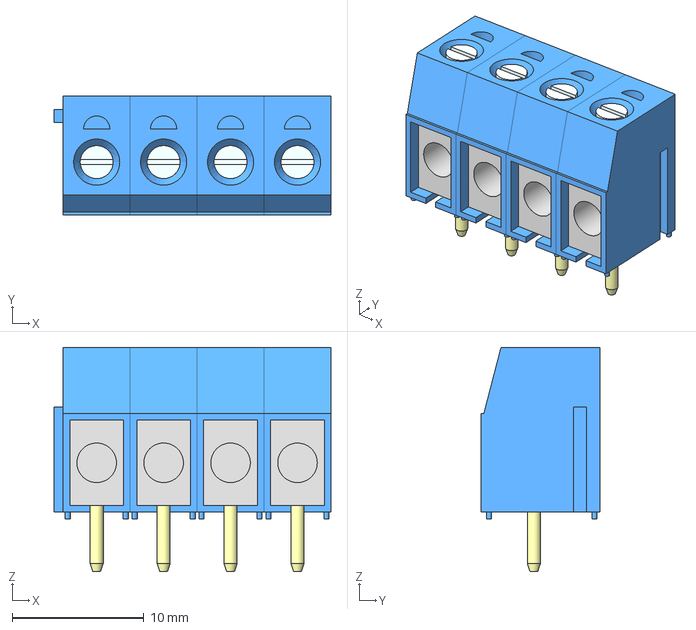
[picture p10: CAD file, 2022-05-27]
pcb/robot/ALTIUM_EMBEDDED_MODELS/ED1204DS.stp
21.0 x 9.00 x 17.0 mm

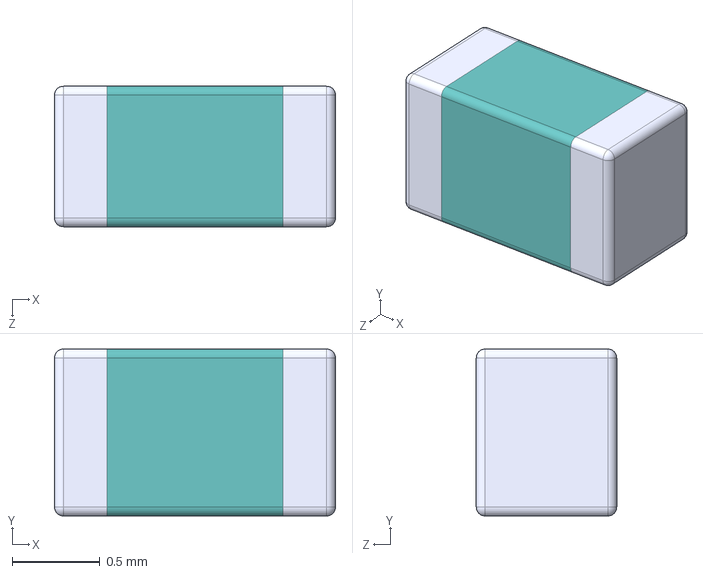
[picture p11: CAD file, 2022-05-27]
pcb/robot/ALTIUM_EMBEDDED_MODELS/IND_C_0603.step
1.60 x 0.95 x 0.8 mm

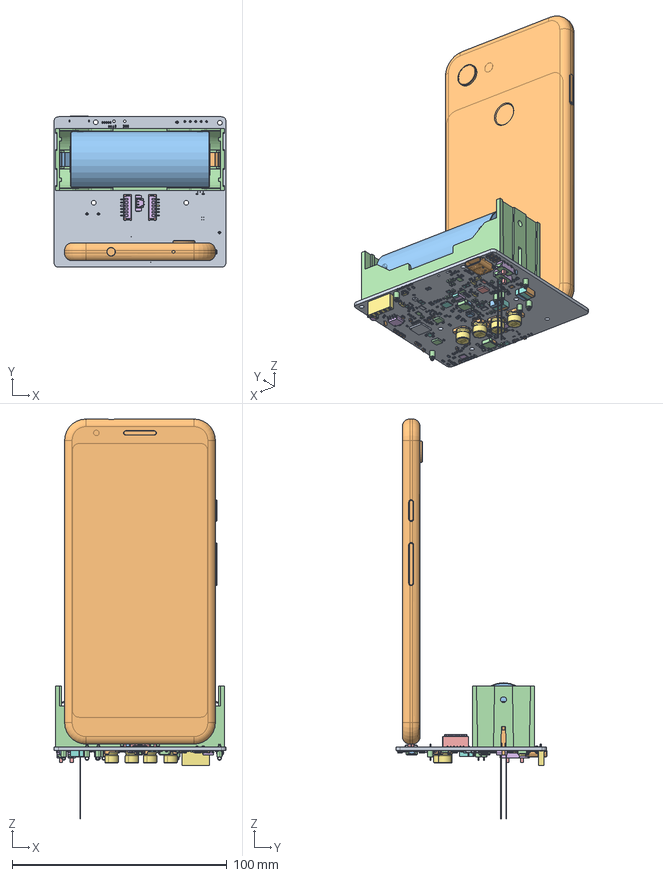
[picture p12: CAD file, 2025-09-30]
body/pcb.FCStd
80.0 x 70.4 x 186.1 mm
Pcb_435
12401832E402A
R85_R_0603_1608Metric_54048ae3dcb1 x 71
C101_C_0603_1608Metric_5cdc6109c0db x 34
R9_R_0402_1005Metric_12ca99383a2d x 19
BODY-SON x 10
D3_MultiTransform_16c11cb9f9c7 x 4
TP3_RCUCTE_e49d1d4a1d4b x 26
C10_C_0402_1005Metric_a75018b17556 x 82
logo
logo001
logo002
logo003
logo004
logo005
logo006
logo007
ball array
ball array001
ball array002
ball array003
ball array004
ball array005
ball array006
ball array007
ball array008
ball array009
ball array010
ball array011
ball array012
ball array013
ball array014
ball array015
ball array016
ball array017
ball array018
ball array019
ball array020
ball array021
ball array022
ball array023
ball array024
ball array025
ball array026
ball array027
74LVC1G11W6-7
74LVC1G11W6-008
74LVC1G11W6-009
74LVC1G11W6-010
74LVC1G11W6-011
74LVC1G11W6-012
74LVC1G11W6-013
74LVC1G11W6-014
42f9e23d-407a-11ed-aca1-3708b1b5f0f2_part
42f9e23e-407a-11ed-aca1-3708b1b5f0f2_part
42f9e23e-407a-11ed-aca1-3708b1b5f0f2_part001
42f9e23e-407a-11ed-aca1-3708b1b5f0f2_part002
42f9e23e-407a-11ed-aca1-3708b1b5f0f2_part003
42f9e23e-407a-11ed-aca1-3708b1b5f0f2_part004
42f9e23e-407a-11ed-aca1-3708b1b5f0f2_part005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

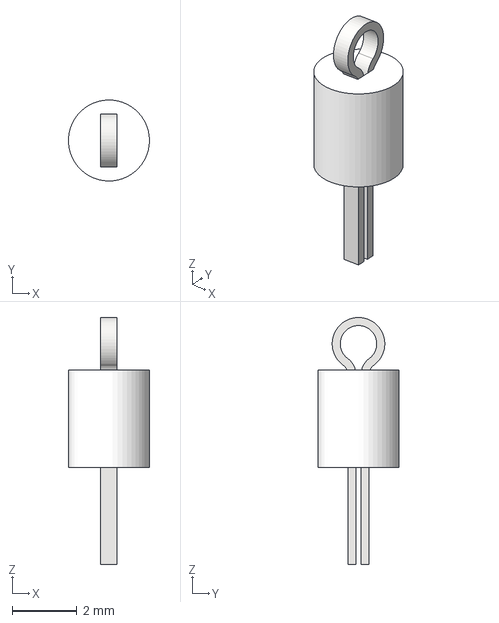
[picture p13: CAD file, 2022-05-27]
pcb/robot/ALTIUM_EMBEDDED_MODELS/Keystone_5002.stp
2.50 x 2.50 x 7.62 mm

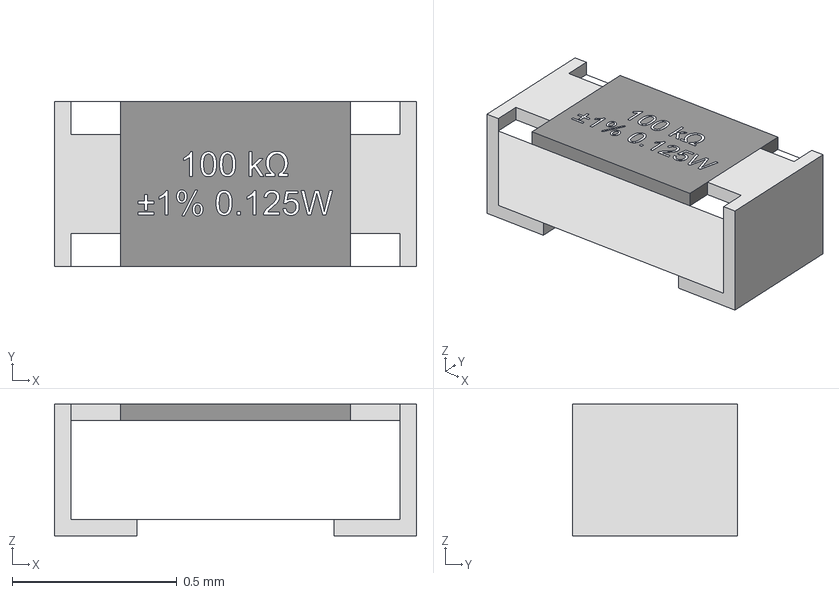
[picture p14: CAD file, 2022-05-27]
pcb/robot/ALTIUM_EMBEDDED_MODELS/Res_TE_CRGP0402F33R_eec.STEP
1.10 x 0.5 x 0.4 mm
terminals
top
value

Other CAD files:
body/electronicAssembly.FCStd
body/bodyAssemblyPrintLayout.FCStd
body/body-Assembly.3mf
body/motorAssembly.FCStd
pcb/robot/ALTIUM_EMBEDDED_MODELS/Keystone_5000.stp
body/Pixel 3A STEP.step
body/RoundedWall.FCStd
body/UMS5_robot3.3mf
body/UMS5_shaft-adapter.3mf
body/battery_footprint.FCStd
body/motor.FCStd
body/smd_leds.FCStd
body/switch.STEP
body/wheel-shaft-adapter.FCStd
body/wheel.FCStd
body/wireless_coil.stp
pcb/robot/ALTIUM_EMBEDDED_MODELS/12401610E4#2A.step
pcb/robot/ALTIUM_EMBEDDED_MODELS/20021111-00010XXLFc.stp
pcb/robot/ALTIUM_EMBEDDED_MODELS/3M_SJ5003Transparent.stp
pcb/robot/ALTIUM_EMBEDDED_MODELS/CAP_C_0402.step
pcb/robot/ALTIUM_EMBEDDED_MODELS/CAP_C_0603.step
pcb/robot/ALTIUM_EMBEDDED_MODELS/Conn_Harwin_M20-9990246_eec.STEP
pcb/robot/ALTIUM_EMBEDDED_MODELS/Conn_Samtec_SNT-100-BK-G_eec.STEP
pcb/robot/ALTIUM_EMBEDDED_MODELS/DBZ0003A.stp
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

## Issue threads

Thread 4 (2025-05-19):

LEDs 1 and 2 are not working on PCBs/firmware

topherbuckley, 2025-05-19:

topherbuckley, 2025-05-19:
This should have been in the firmware repo.

Closed 2025-05-19.

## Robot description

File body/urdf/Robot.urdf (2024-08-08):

<?xml version="1.0" ?>
<robot name="Robot">
  <!--Generated by CROSS, a ROS Workbench for FreeCAD (https://github.com/galou/freecad.cross)-->
  <link name="Link023">
    <inertial>
      <mass value="0.0"/>
      <origin xyz="0.0 0.0 0.0" rpy="0.0 -0.0 0.0"/>
      <inertia ixx="0.0" ixy="0.0" ixz="0.0" iyy="0.0" iyz="0.0" izz="0.0"/>
    </inertial>
  </link>
  <link name="Link030">
    <inertial>
      <mass value="0.0"/>
      <origin xyz="0.0 0.0 0.0" rpy="0.0 -0.0 0.0"/>
      <inertia ixx="0.0" ixy="0.0" ixz="0.0" iyy="0.0" iyz="0.0" izz="0.0"/>
    </inertial>
  </link>
  <link name="Link031">
    <inertial>
      <mass value="0.0"/>
      <origin xyz="0.0 0.0 0.0" rpy="0.0 -0.0 0.0"/>
      <inertia ixx="0.0" ixy="0.0" ixz="0.0" iyy="0.0" iyz="0.0" izz="0.0"/>
    </inertial>
  </link>
  <joint name="Joint" type="revolute">
    <parent link="Link023"/>
    <child link="Link030"/>
    <origin xyz="-0.05384 -0.01395 -0.0085" rpy="0.0 -0.0 0.0"/>
    <axis xyz="0 0 1"/>
    <limit lower="0.0" upper="0.0" velocity="0.0" effort="0.0"/>
  </joint>
  <joint name="Joint001" type="revolute">
    <parent link="Link023"/>
    <child link="Link031"/>
    <origin xyz="0.05384 -0.01395 -0.0085" rpy="0.0 -0.0 0.0"/>
    <axis xyz="0 0 1"/>
    <limit lower="0.0" upper="0.0" velocity="0.0" effort="0.0"/>
  </joint>
</robot>

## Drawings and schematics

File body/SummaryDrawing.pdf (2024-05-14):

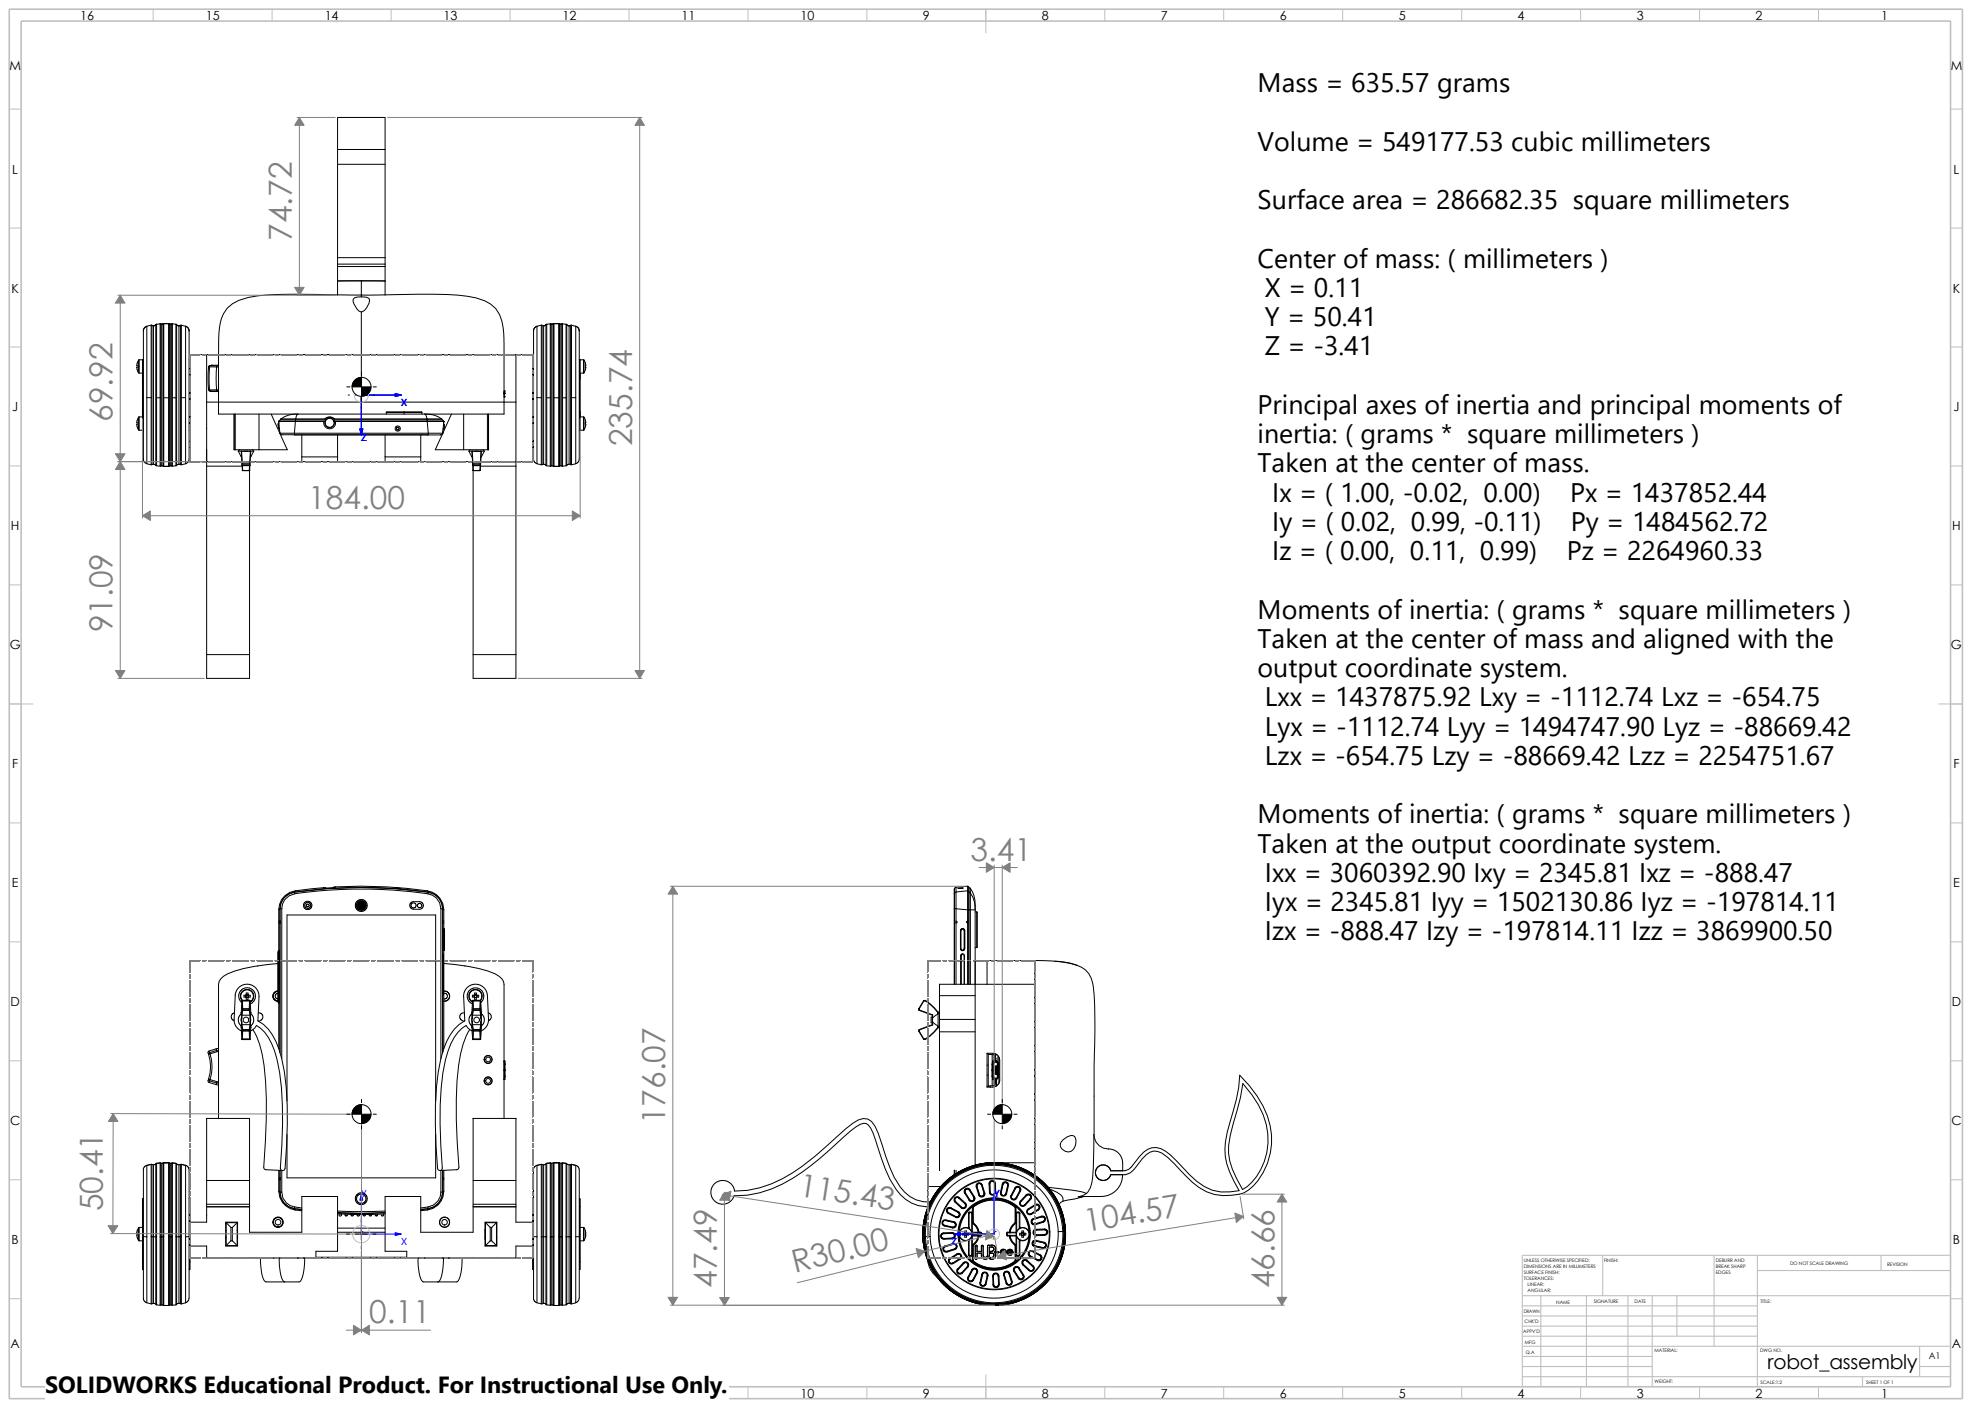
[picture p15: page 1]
FINISH:; EDGES; DO NOT SCALE DRAWING; REVISION; SCALE:1:2; SHEET 1 OF 1; WEIGHT:; DEBURR AND BREAK SHARP; Mass = 635.57 grams; Center of mass: ( millimeters ) X = 0.11 Y = 50.41 Z = -3.41

Volume = 549177.53 cubic millimeters

Surface area = 286682.35 square millimeters

Principal axes of inertia and principal moments of
inertia: ( grams * square millimeters )
Taken at the center of mass.

Moments of inertia: ( grams * square millimeters )
Taken at the center of mass and aligned with the
output coordinate system.
Lxx = 1437875.92 Lxy = -1112.74 Lxz = -654.75
Lyx = -1112.74 Lyy = 1494747.90 Lyz = -88669.42
Lzx = -654.75 Lzy = -88669.42 Lzz = 2254751.67

Taken at the output coordinate system.
Ixx = 3060392.90 Ixy = 2345.81 Ixz = -888.47
Iyx = 2345.81 Iyy = 1502130.86 Iyz = -197814.11
Izx = -888.47 Izy = -197814.11 Izz = 3869900.50 46.66

UNLESS OTHERWISE SPECIFIED:
DIMENSIONS ARE IN MILLIMETERS
SURFACE FINISH:
TOLERANCES:
LINEAR:
ANGULAR:

NAME | SIGNATURE | DATE | | | | TITLE:

DRAWN

CHK'D

APPV'D

SOLIDWORKS Educational Product. For Instructional Use Only.

MFG

Q.A | | | | MATERIAL: | DWG NO. robot_assembly | A1

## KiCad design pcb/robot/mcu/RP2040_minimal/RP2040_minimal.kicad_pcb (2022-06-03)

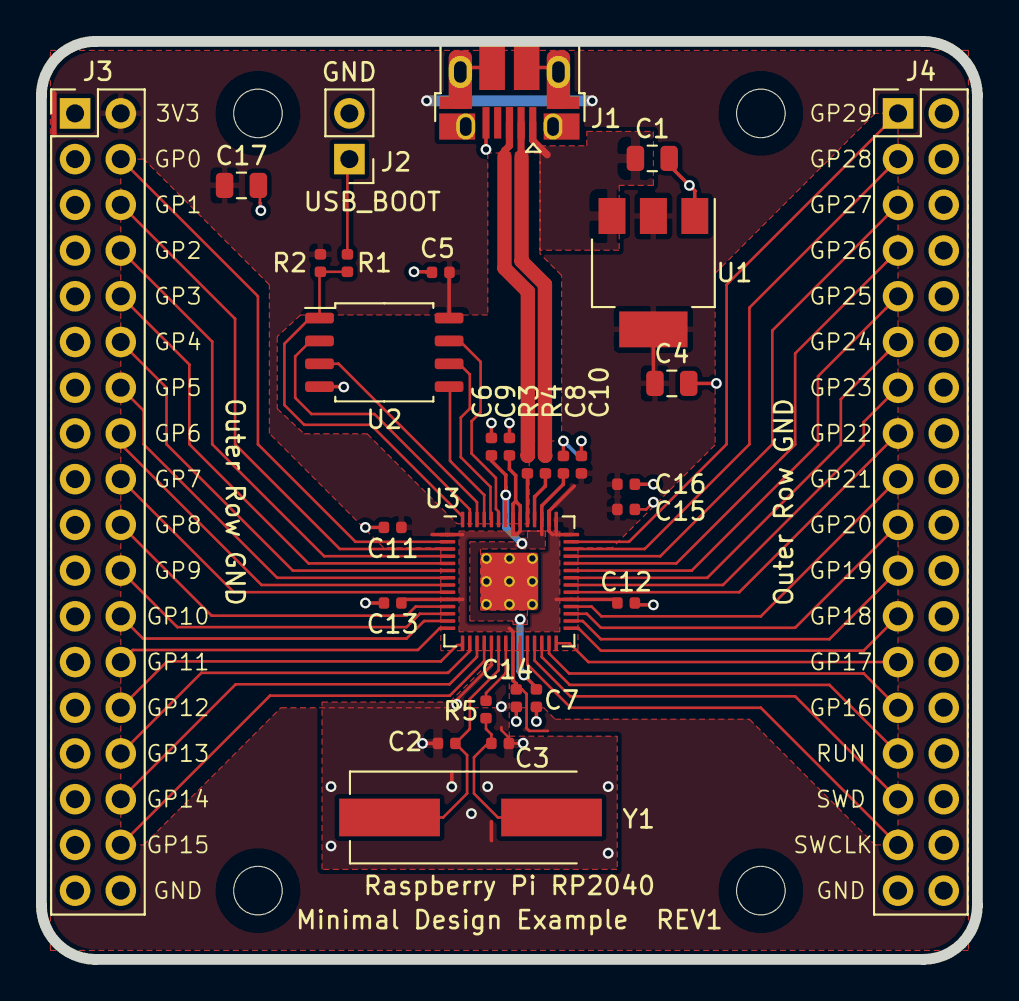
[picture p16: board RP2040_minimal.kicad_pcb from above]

Board: 2 copper layers, 52.0 x 51.0 mm, 34 parts (0 on the bottom side), 51 nets.

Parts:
C1, C4, C17: 10u; C_0805_2012Metric
C2, C3: 27p; C_0402_1005Metric
C5, C6, C7, C9, C11, C12, C13, C14, C15, C16: 100n; C_0402_1005Metric
C8, C10: 1u; C_0402_1005Metric
H1, H2, H3, H4: MountingHole; MountingHole_2.7mm_M2.5
J1: USB_B_Micro; USB_Micro-B_Amphenol_10103594-0001LF_Horizontal_modified
J2: Conn_01x02; PinHeader_1x02_P2.54mm_Vertical
J3, J4: Conn_02x18_Odd_Even; PinHeader_2x18_P2.54mm_Vertical
R1, R5: 1k; C_0402_1005Metric
R2: DNF; C_0402_1005Metric
R3, R4: 27; C_0402_1005Metric
U1: NCP1117-3.3_SOT223; SOT-223-3_TabPin2
U2: W25Q128JVS; SOIC-8_5.23x5.23mm_P1.27mm
U3: RP2040; RP2040-QFN-56
Y1: ABLS-12.000MHZ-B4-T; Crystal_SMD_HC49-US

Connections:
+1V1: C6.1, C7.1, C8.1, U3.23, U3.45, U3.50
+3V3: C4.1, C5.1, C9.1, C10.1, C11.1, C12.1, C13.1, C14.1, C15.1, C16.1, C17.1, J3.2, R2.1, U1.2, U2.8, U3.1, U3.10, U3.22, U3.33, U3.42, U3.43, U3.44, U3.48, U3.49
/GPIO0: J3.4, U3.2
/GPIO1: J3.6, U3.3
/GPIO2: J3.8, U3.4
/GPIO3: J3.10, U3.5
/GPIO4: J3.12, U3.6
/GPIO5: J3.14, U3.7
/GPIO6: J3.16, U3.8
/GPIO7: J3.18, U3.9
/GPIO8: J3.20, U3.11
/GPIO9: J3.22, U3.12
/GPIO10: J3.24, U3.13
/GPIO11: J3.26, U3.14
/GPIO12: J3.28, U3.15
/GPIO13: J3.30, U3.16
/GPIO14: J3.32, U3.17
/GPIO15: J3.34, U3.18
/GPIO16: J4.27, U3.27
/GPIO17: J4.25, U3.28
/GPIO18: J4.23, U3.29
/GPIO19: J4.21, U3.30
/GPIO20: J4.19, U3.31
/GPIO21: J4.17, U3.32
/GPIO22: J4.15, U3.34
/GPIO23: J4.13, U3.35
/GPIO24: J4.11, U3.36
/GPIO25: J4.9, U3.37
/GPIO26_ADC0: J4.7, U3.38
/GPIO27_ADC1: J4.5, U3.39
/GPIO28_ADC2: J4.3, U3.40
/GPIO29_ADC3: J4.1, U3.41
/QSPI_SCLK: U2.6, U3.52
/QSPI_SD0: U2.5, U3.53
/QSPI_SD1: U2.2, U3.55
/QSPI_SD2: U2.3, U3.54
/QSPI_SD3: U2.7, U3.51
/QSPI_SS: R1.1, R2.2, U2.1, U3.56
/RUN: J4.29, U3.26
/SWCLK: J4.33, U3.24
/SWD: J4.31, U3.25
/USB_D+: J1.3, R3.1
/USB_D-: J1.2, R4.1
/XIN: C2.1, U3.20, Y1.1
/XOUT: R5.1, U3.21
/~USB_BOOT: J2.1, R1.2
GND: C1.2, C2.2, C3.2, C4.2, C5.2, C6.2, C7.2, C8.2, C9.2, C10.2, C11.2, C12.2, C13.2, C14.2, C15.2, C16.2, C17.2, J1.5, J1.6, J2.2, J3.1, J3.3, J3.5, J3.7, J3.9, J3.11, J3.13, J3.15, J3.17, J3.19, J3.21, J3.23, J3.25, J3.27, J3.29, J3.31, J3.33, J3.35, J3.36, J4.2, J4.4, J4.6, J4.8, J4.10, J4.12, J4.14, J4.16, J4.18, J4.20, J4.22, J4.24, J4.26, J4.28, J4.30, J4.32, J4.34, J4.35, J4.36, U1.1, U2.4, U3.19, U3.57
unnamed: C3.1, R5.2, Y1.2
unnamed: R3.2, U3.47
unnamed: R4.2, U3.46
VBUS: C1.1, J1.1, U1.3

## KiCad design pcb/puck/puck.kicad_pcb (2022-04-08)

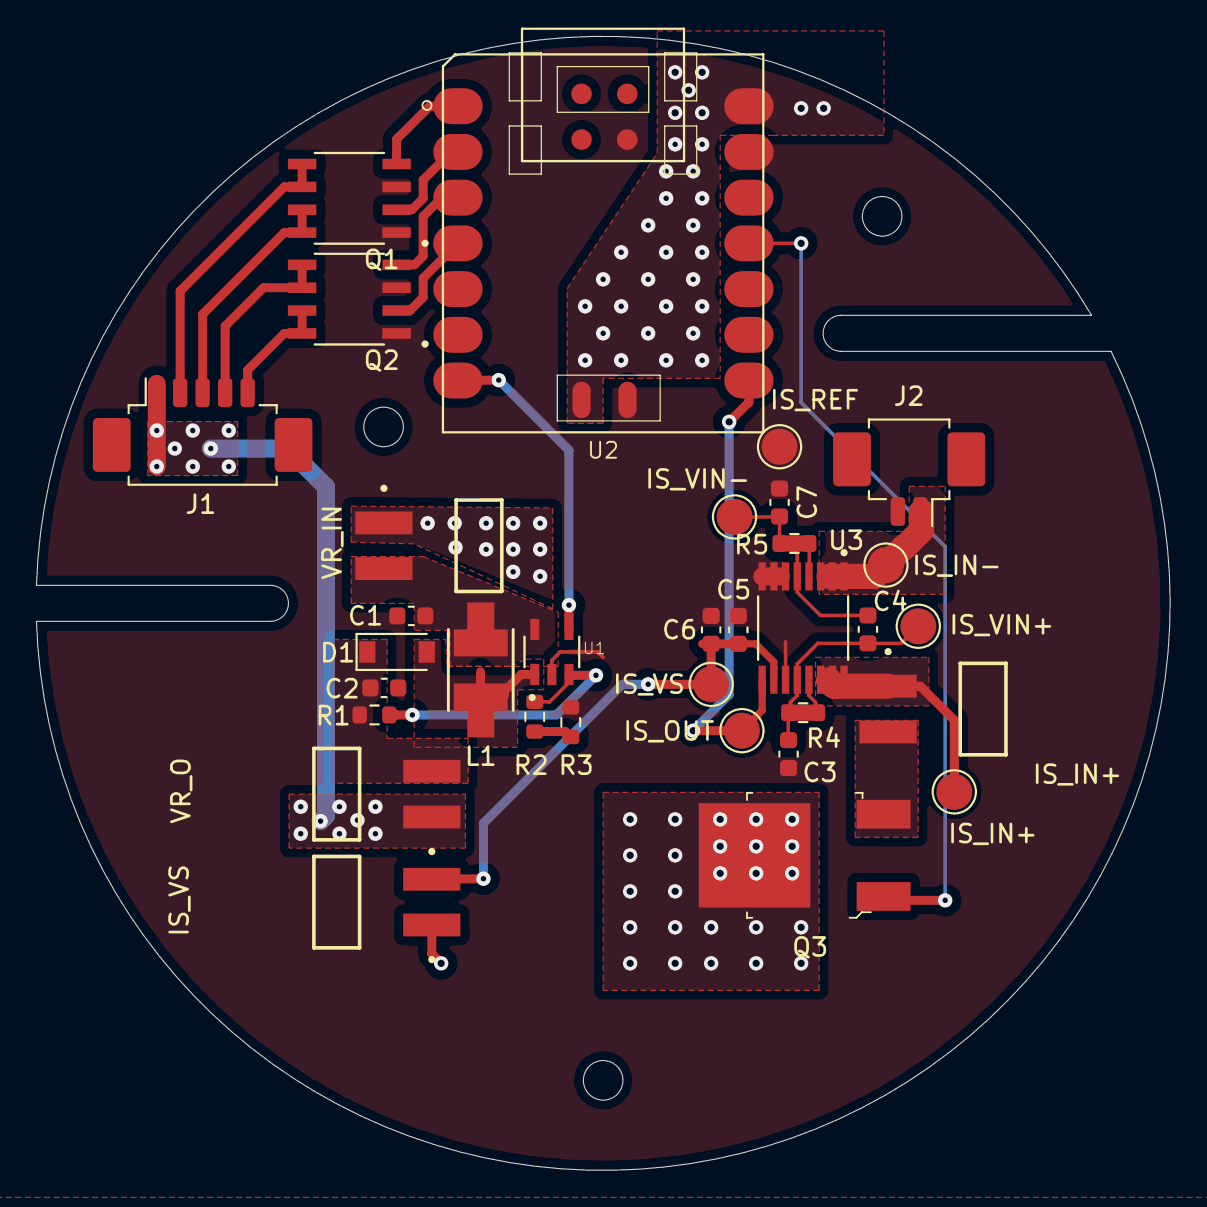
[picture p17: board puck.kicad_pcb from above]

Board: 2 copper layers, 63.0 x 63.0 mm, 33 parts (0 on the bottom side), 27 nets.

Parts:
C1, C2, C6: C_1uF; C_0603_1608Metric
C3, C4, C7: DNP; C_0603_1608Metric_DNP
C5: C_0.1uF; C_0603_1608Metric
D1: 1N5819; D_SOD-123
J1: PicoBlade_5Pin_SMD_Horizontal; Molex_PicoBlade_53261-0571_1x05-1MP_P1.25mm_Horizontal
J2: PicoBlade_2Pin_SMD_Horizontal; Molex_PicoBlade_53261-0271_1x02-1MP_P1.25mm_Horizontal
L1: 10u; IND_LQH43PN100M26L
Q1, Q2: DMN3018SSD-13; SOIC127P600X170-8N
Q3: IRLR6225TRPBF; TO-252-3
R1: 21.5k; R_0603_1608Metric
R2: 1.37k; R_0603_1608Metric
R3: 1.13k; R_0603_1608Metric
R4, R5: NetTie; R_0603_1608Metric_NetTie
TP1, TP2, TP3, TP4, TP5, TP6, TP7: TestPoint_SMDpad; TestPoint_Pad_D2.0mm
TP8, TP9, TP10, TP11: TestPoint_CurrentShunt; SAMTEC_TSM-102-01-T-SH
U1: AP3012KTR-G1; SOT95P280X145-5N
U2: SeeeduinoXIAO; Seeeduino_XIAO-MOUDLE14P-2p54-21X17p8MM
U3: INA250A3PWR; SOP65P640X120-16N

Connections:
+5V: Q3.4, TP10.1, TP11.1, U2.13
/12vRegulator/Vin: C1.1, L1.1, TP11.2, U1.5
/12vRegulator/Vout: C2.1, D1.1, R1.1, TP8.2
/currentSense/IN+: TP3.1, TP9.1, U3.14, U3.15, U3.16
/currentSense/OUT: TP7.1, U2.7, U3.9
/currentSense/VS: C5.2, C6.2, TP4.1, TP10.2, U3.10
GND: C1.2, C2.2, C3.2, C5.1, C6.1, C7.2, J2.2, Q1.1, Q1.3, Q2.1, Q2.3, R3.2, TP1.1, U1.2, U2.12, U3.6, U3.7, U3.8, U3.11
LED_B: J1.4, Q2.5, Q2.6
LED_B_IO: Q2.4, U2.2
LED_G: J1.3, Q1.7, Q1.8
LED_G_IO: Q1.2, U2.1
LED_R: J1.2, Q1.5, Q1.6
LED_R_IO: Q1.4, U2.0
LED_W: J1.5, Q2.7, Q2.8
LED_W_IO: Q2.2, U2.3
unnamed: C3.1, C4.1, R4.1, TP2.1, U3.12
unnamed: C4.2, C7.1, R5.2, TP6.1, U3.5
unnamed: D1.2, L1.2, U1.1
unnamed: J1.1, TP8.1
unnamed: Q3.1, U2.10
unnamed: Q3.3, TP9.2
unnamed: R1.2, R2.1, U1.3
unnamed: R2.2, R3.1
unnamed: R4.2, U3.13
unnamed: R5.1, U3.4
SHDN: U1.4, U2.6
WirelssModule_Vin: J2.1, TP5.1, U3.1, U3.2, U3.3

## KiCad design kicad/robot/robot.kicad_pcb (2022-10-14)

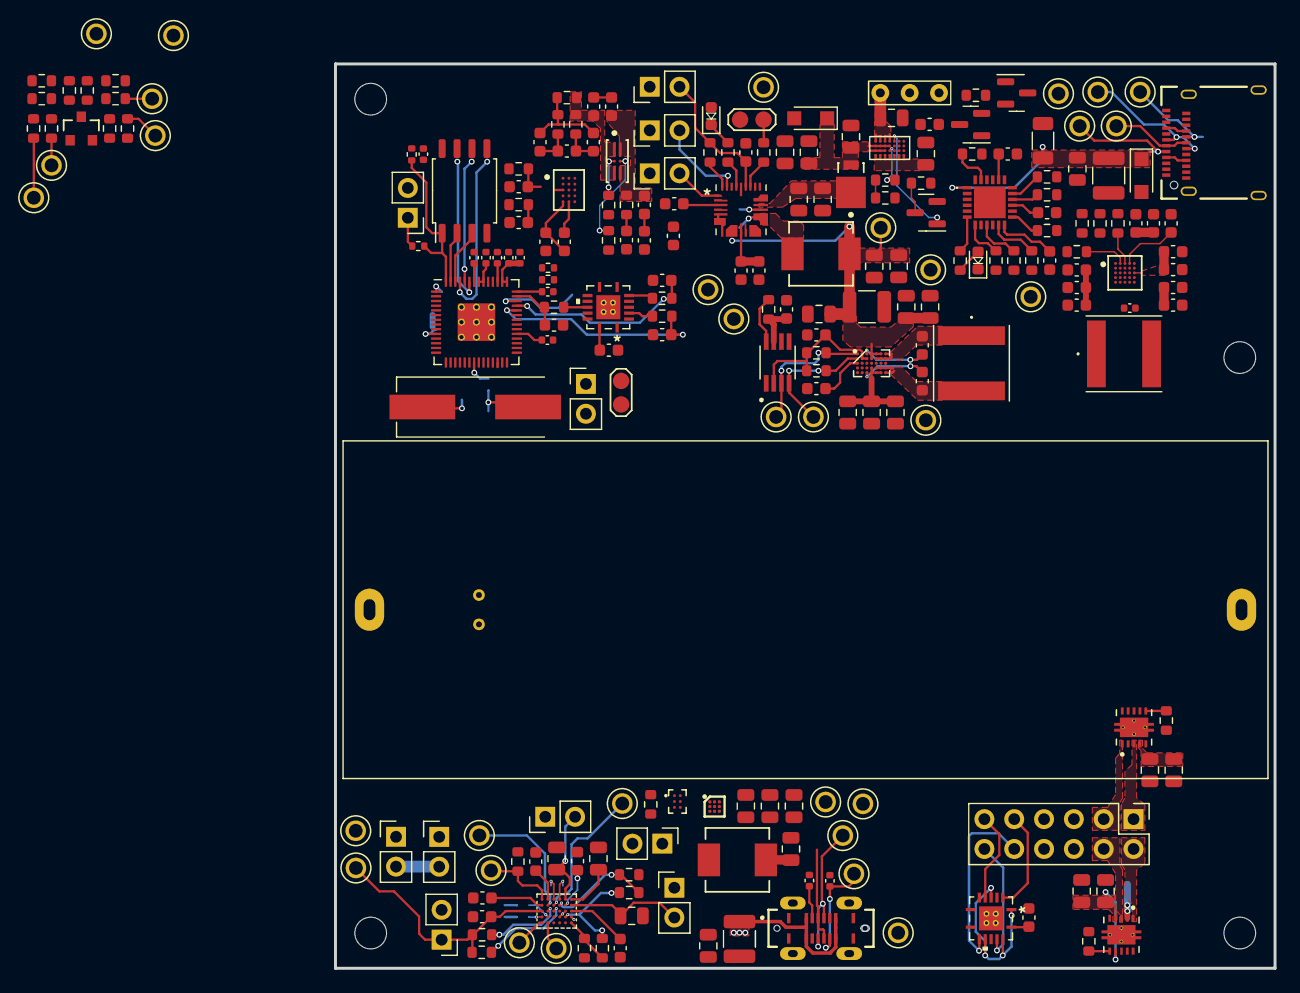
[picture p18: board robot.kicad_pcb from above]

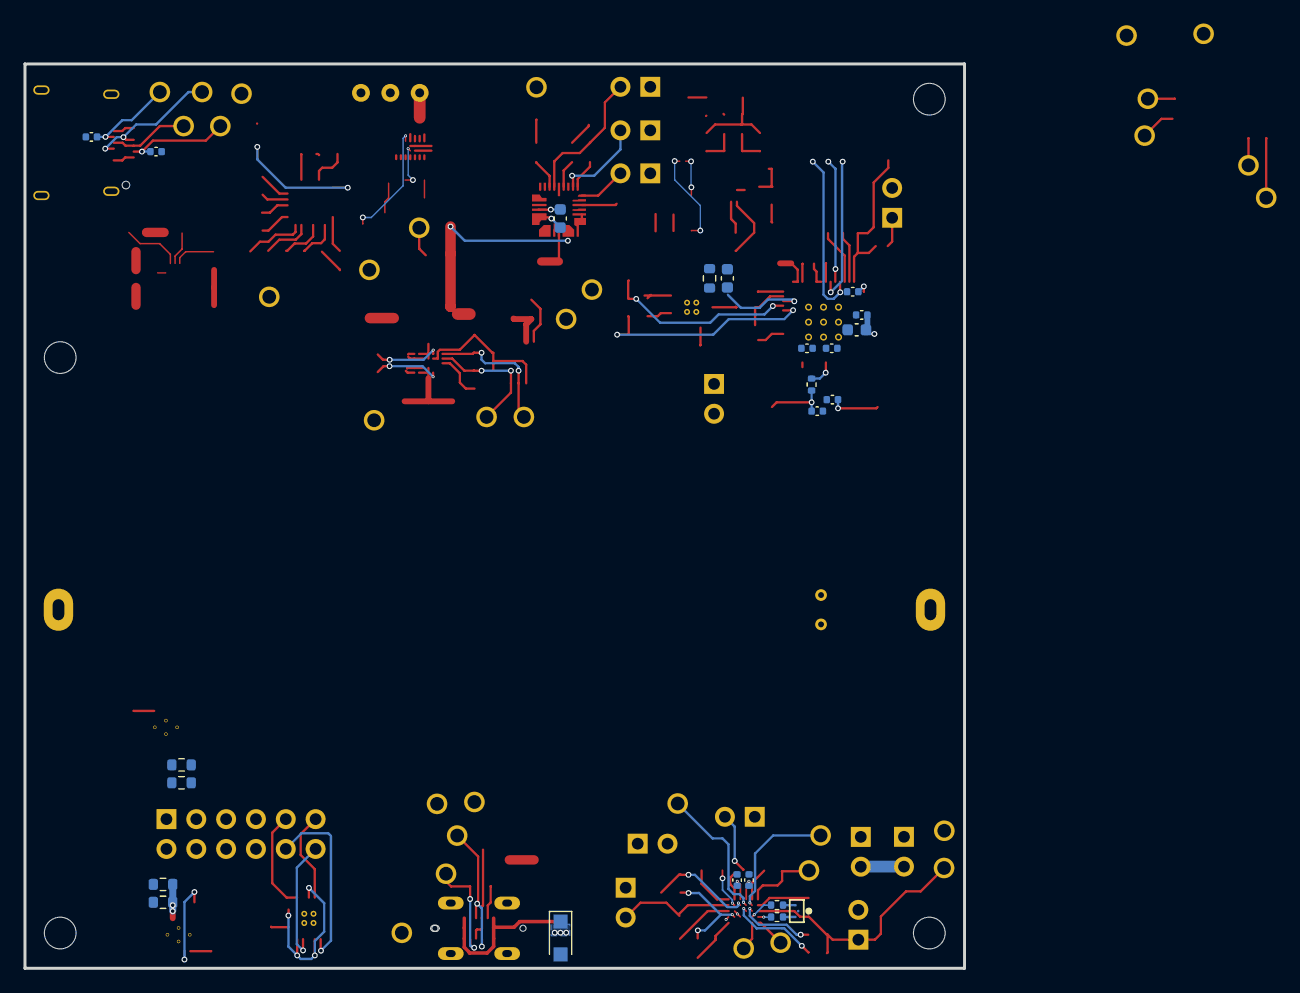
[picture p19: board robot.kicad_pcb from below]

Board: 4 copper layers, 80.0 x 77.0 mm, 254 parts (23 on the bottom side), 156 nets.

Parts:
BT1: DNP; battery26650_thermistor
C1, C94, C96: 100uF; C_1210_3225Metric
C2, C3: 27p; C_0402_1005Metric
C4, C51, C52, C53, C54, C55, C69, C88, C105: 1uF; C_0603_1608Metric
C5, C6, C7, C9, C11, C12, C13, C14, C15, C16: 100n; C_0402_1005Metric
C8, C10: 1u; C_0402_1005Metric
C17: 10u; C_0603_1608Metric
C18, C19, C45, C46, C89, C95: 27pF; C_0402_1005Metric
C20, C97: 2.2uF; C_0805_2012Metric
C21, C22, C47, C48, C50: 1uF; C_0805_2012Metric
C23, C98, C99, C101: 4.7uF; C_0805_2012Metric
C24, C36, C37, C38, C39, C70, C71, C72, C73, C74, C85, C90, C92: 100nF; C_0603_1608Metric
C25, C27, C42, C43, C67, C68, C77, C80, C100: 10uF; C_0805_2012Metric
C26, C56: 0.47uF; C_0603_1608Metric
C28, C49: 2.2uF; C_0603_1608Metric
C29, C32, C40, C41: 100nF; C_0805_2012Metric
C30, C31: 0.22uF; C_0603_1608Metric
C33, C34, C76, C78: 22uF; C_0805_2012Metric
C35, C44, C57, C58, C59, C60, C61, C62, C63, C64, C65, C66, C102, C103, C104: 0.1uF; C_0603_1608Metric
C75: 10uF; C_0603_1608Metric
C84: 10nF; C_0402_1005Metric
C86, C87, C91, C93: 22uF; C_0603_1608Metric
D1: AZ23C5V6-7-F; Diodes_Inc-SOT23-01_2017-0-MFG
D2, D3, D5: PTVS20VS1UR; Nexperia_CFP3_SOD-123W
D4, D6: LED; D_0603_1608Metric_Harvatek
D7: D_Schottky; Vishay-SS1P3L-M3_84A-0-0-0
H1, H2, H3, H4: MountingHole; MountingHole_2.7mm_M2.5
IC1: TPS61253AYFFR; Texas_Instruments-YFF0009-BGA9C40P3X3_119X129X62
IC2: AP33771DKZ-13; AP33771DKZ13
IN1: TestPoint; KEYSTONE_5002
J1: USBC_Receptacle_SMD_RA; CON_USB3.1-C_RCPT_SMD_RA_ACP_12401610E4#2A
J2: Conn_01x02; PinHeader_1x02_P2.54mm_Vertical
J3: 67996-412HLF; PinHeader_2x06_P2.54mm_Vertical
J4: USB4120-03-C_REVA; GCT_USB4120-03-C_REVA
JP1, JP7: 76VIO; 2.54mm_2pointCurrentTestPoint
JP2: 58VCIN; 2.54mm_2pointCurrentTestPoint
JP3: 58SYS; 2.54mm_2pointCurrentTestPoint
JP4: 58VBUS; 2.54mm_2pointCurrentTestPoint
JP5: 58VIO2; 2.54mm_2pointCurrentTestPoint
JP6: 58VIO1; 2.54mm_2pointCurrentTestPoint
JP8: 76SUSPND; 2.54mm_2pointCurrentTestPoint
JP9: 76DISQBAT; 2.54mm_2pointCurrentTestPoint
L1, L3: 1.5uH; NRS6028T1R5NMGJ
L2, L4: 0.47uH; Vishay-IHLP-2020BZ-FP_1.905x2.79-3D_2.0-0-0-MFG
OUT1: TestPoint; KEYSTONE_5002
PGND1: TestPoint; KEYSTONE_5002
Q1: Q_NMOS_GDS; SOT-23
Q2: EFC8811R-TF; ON_Semiconductor-568AL-10_2013-O-MFG
Q3, Q4: YJL3416A; SOT-23
R1, R5: 1k; R_0402_1005Metric
R2: DNF; R_0402_1005Metric
R3, R4: 27; R_0402_1005Metric
R6, R7: 0; R_0603_1608Metric
R8, R9, R12, R13, R22, R23, R24, R25, R58: 100; R_0603_1608Metric
R10, R11, R14, R15, R46, R47, R50: 1k; R_0603_1608Metric
R16: 510k; R_0603_1608Metric
R17, R49, R59, R60, R61: 100k; R_0603_1608Metric
R18: 47K; R_0603_1608Metric
R19, R36: 200k; R_0603_1608Metric
R20, R21, R34, R35: 2.2k; R_0603_1608Metric
R26, R27, R66: DNP; R_0603_1608Metric
R28, R31, R57: 10k; R_0603_1608Metric
R29, R30: 0.4; R_0603_1608Metric
R32, R33: 1; R_0402_1005Metric
R37, R39: 649k; R_0603_1608Metric
R38, R40: 120k; R_0603_1608Metric
R41, R42, R56: 10; R_0603_1608Metric
R43, R45: 200; R_0603_1608Metric
R44: 5m; R_0603_1608Metric
R48: 2k; R_0603_1608Metric
R51: 10m; R_1206_3216Metric
R52: 768k; R_0603_1608Metric
R53: 113K; R_0603_1608Metric
R54: 28k; R_0603_1608Metric
R55: 14k; R_0603_1608Metric
R62: 16k; R_0603_1608Metric
R63, R64: 5.1k; R_0603_1608Metric
R65: 10M; R_0603_1608Metric
SCL1V1: TestPoint; KEYSTONE_5002
SDA1V1: TestPoint; KEYSTONE_5002
TP1: SDA_SL; KEYSTONE_5002
TP2: SCL_SL; KEYSTONE_5002
TP3: I2C0_SDA; KEYSTONE_5002
TP4: I2C0_SCL; KEYSTONE_5002
TP5: SDA_EXT; KEYSTONE_5002
TP6: SCL_EXT; KEYSTONE_5002
TP7, TP13: D-; KEYSTONE_5002
TP8, TP14: D+; KEYSTONE_5002
TP9, TP15: CC1; KEYSTONE_5002
TP10, TP29: CC2; KEYSTONE_5002
TP11, TP30: VBUS; KEYSTONE_5002
TP12, TP28: SWD; TestPoint_2Pads_Pitch2mm_SMD
TP16, TP17, TP18, TP19, TP20, TP21, TP22, TP23, TP24, TP25, TP26: TestPoint; KEYSTONE_5002
TP27: SWD; 2.54mm_2pointCurrentTestPoint
U1: WRM483265-10F5-12V-G
U2: W25Q128JVS; SOIC-8_5.23x5.23mm_P1.27mm
U3: RP2040; RP2040-QFN-56
U4: NCP3901
U5: LSF0102DCTR; SOP65P400X130-8N
U6: MAX77857; WLP-35_7x5_2.828x2.028mm
U7, U10: SN74AHC125RGYR
U8, U9: DRV8830DRCR; IC_DRV8830DRCR
U11: MAX77958EWV+T; MAX77958EWV&plus_T
U12: BQ27742YZFR-G1; Texas_Instruments-YZF0015-0-0-MFG
U13: MAX77976EFD+; MAX77976
U14: MAX77642ANA+; Maxim-N252B2-1-0-A-MFG
U15: ESD122DMYR; Texas_Instruments-DMY0003A-0-0-MFG
U16: fpf1048bucx; BGA6N50P3X2_146X96X62N
Y1: ABLS-12.000MHZ-B4-T; Crystal_SMD_HC49-US

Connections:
/1V8: C26.1, C74.1, C86.1, R20.1, R21.1, U5.2 (VREF_A), U6.A2 (VIO), U6.B2 (EN), U6.B3 (EN), U14.D3 (SBB2)
/3V3: C5.1, C9.1, C10.1, C11.1, C12.1, C13.1, C14.1, C15.1, C16.1, C17.1, C24.1, C35.1, C44.1, C92.1, C93.1, JP1.1 (A), JP5.2 (B), JP7.1 (A), JP8.1 (A), JP9.1 (A), R2.1, R10.1, R11.1, R14.1, R15.1, R18.1, R19.1, R28.1, R31.1, U2.8 (VCC), U3.1 (IOVDD), U3.10 (IOVDD), U3.22 (IOVDD), U3.33 (IOVDD), U3.42 (IOVDD), U3.43 (ADC_AVDD), U3.44 (VREG_IN), U3.48 (USB_VDD), U3.49 (IOVDD), U5.7 (VREF_B), U7.14 (VCC), U10.14 (VCC), U14.C3 (SBB1)
/5V: C90.1, C91.1, J3.7, J3.8, U14.C5 (SBB0)
/ADC0: R16.2, R17.1, U7.2 (1A)
/Charger/BATT: C63.2, C65.1, C75.1, Q2.4 (SOURCE2), Q2.6 (SOURCE2), R48.1, TP12.2, TP24.1, U13.5 (BATSP), U13.6 (BATT), U13.7 (BATT), U13.8 (BATT)
/Charger/PVDD: C69.1, C70.1, U13.12 (PVDD)
/Charger/V_IN: C23.1, C67.1, C68.1, D5.1 (K), D7.2 (Anode), TP23.1, U4.B5 (OUT), U4.B6 (OUT), U4.B7 (OUT), U4.C4 (OUT), U4.C5 (OUT), U4.C6 (OUT), U4.C7 (OUT), U13.22 (CHGIN), U13.23 (CHGIN)
/GPIO4: Q1.3 (D), R18.2, U3.6 (GPIO4)
/GPIO5: U3.7 (GPIO5), U4.D2 (VINA_EN/OTG_EN)
/GPIO6: R49.2, U3.8 (GPIO6), U13.32 (IRQB)
/GPIO7: R36.2, TP20.1, U3.9 (GPIO7), U11.A1 (INTB)
/GPIO9: U1.3 (WC_EN), U3.12 (GPIO9)
/GPIO10: R28.2, U3.13 (GPIO10), U8.6 (~FAULT)
/GPIO11: R31.2, U3.14 (GPIO11), U9.6 (~FAULT)
/GPIO12: U3.15 (GPIO12), U10.3 (1Y)
/GPIO13: U3.16 (GPIO13), U10.6 (2Y)
/GPIO14: U3.17 (GPIO14), U10.8 (3Y)
/GPIO15: U3.18 (GPIO15), U10.11 (4Y)
/GPIO16: U3.27 (GPIO16), U10.1 (1~OE), U10.4 (2~OE), U10.10 (3~OE), U10.13 (4~OE)
/I2C0_SCL: R15.2, TP4.1, U3.3 (GPIO1), U5.6 (B1), U8.10 (SCL), U9.10 (SCL), U12.E3 (SCL)
/I2C0_SDA: R14.2, TP3.1, U3.2 (GPIO0), U5.5 (B2), U8.9 (SDA), U9.9 (SDA), U12.C3 (SDA)
/I2C1_SCL: R35.2, U3.5 (GPIO3), U11.C2 (SCL_M), U13.24 (SCL)
/I2C1_SDA: R34.2, U3.4 (GPIO2), U11.C3 (SDA_M), U13.25 (SDA)
/MCU/GPIO26_ADC0: C39.1, R25.1, U3.38 (GPIO26_ADC0)
/MCU/GPIO27_ADC1: C38.1, R24.1, U3.39 (GPIO27_ADC1)
/MCU/GPIO28_ADC2: C37.1, R23.1, U3.40 (GPIO28_ADC2)
/MCU/GPIO29_ADC3: C36.1, R22.1, U3.41 (GPIO29_ADC3)
/MCU/QSPI_SCLK: U2.6 (CLK), U3.52 (QSPI_SCLK)
/MCU/QSPI_SD0: U2.5 (DI(IO0)), U3.53 (QSPI_SD0)
/MCU/QSPI_SD1: U2.2 (DO(IO1)), U3.55 (QSPI_SD1)
/MCU/QSPI_SD2: U2.3 (IO2), U3.54 (QSPI_SD2)
/MCU/QSPI_SD3: U2.7 (IO3), U3.51 (QSPI_SD3)
/MCU/QSPI_SS: R1.1, R2.2, U2.1 (~CS), U3.56 (QSPI_SS)
/MCU/RUN: TP28.1, U3.26 (RUN)
/MCU/SWCLK: TP27.2, U3.24 (SWCLK)
/MCU/SWD: TP27.1, U3.25 (SWD)
/MCU/XIN: C2.1, U3.20 (XIN), Y1.1
/MCU/XOUT: R5.1, U3.21 (XOUT)
/MCU/~USB_BOOT: J2.1, R1.2
/MOTORS/ENC_11: J3.9, U10.2 (1A)
/MOTORS/ENC_12: J3.11, U10.5 (2A)
/MOTORS/ENC_21: J3.10, U10.9 (3A)
/MOTORS/ENC_22: J3.12, U10.12 (4A)
/MOTORS/OUT_N1: J3.3, U8.1 (OUT2)
/MOTORS/OUT_N2: J3.2, U9.1 (OUT2)
/MOTORS/OUT_P1: J3.1, U8.3 (OUT1)
/MOTORS/OUT_P2: J3.4, U9.3 (OUT1)
/PowerMux/FLAG: Q1.1 (G), U4.D3 (VINB_EN/FLAG)
/PowerMux/VIN_A: C21.1, C105.1, IC2.22 (VBUS), Q4.3 (D), U4.A1 (VINA), U4.A2 (VINA), U4.A3 (VINA), U4.A4 (VINA), U4.A5 (VINA), U4.A6 (VINA), U4.A7 (VINA)
/PowerMux/VIN_B: C22.1, U1.1 (Vchar_IN), U4.D4 (VINB), U4.D5 (VINB), U4.D6 (VINB), U4.D7 (VINB)
/SCL_SL: R7.1, TP2.1, TP19.1, U11.B3 (SDA)
/SDA_SL: R6.1, TP1.1, TP18.1, U11.B2 (SCL)
/SYS: C1.1, C4.1, C25.1, C27.1, C29.2, C76.1, C78.1, C85.1, C87.1, C101.1, D6.2 (A), IC1.A3 (VIN), IN1.1, JP2.1 (A), JP3.1 (A), L2.2, L4.1, TP25.1, U6.A4 (IN), U6.A5 (IN), U6.A6 (IN), U6.B4 (IN), U13.9 (SYS), U13.10 (SYS), U13.11 (SYS), U14.A1 (SYSA), U14.A5 (IN_LDO), U14.B1 (SYSA), U14.D1 (EN1), U14.D2 (EN0), U14.E1 (EN2), U14.E3 (IN_SBB)
/USB-C_ExtChg/CC1: C18.1, IC2.17 (CC1), J1.A5 (CC1), R63.1, TP9.1
/USB-C_ExtChg/CC2: C19.1, IC2.16 (CC2), J1.B5 (CC2), R64.1, TP10.1
/USB-C_ExtChg/D+: J1.A6 (D+), J1.B6 (D+), TP8.1
/USB-C_ExtChg/D-: J1.A7 (D-), J1.B7 (D-), TP7.1
/USB-C_ExtChg/VBUS: C20.1, C94.1, D2.1 (K), IC2.1 (ISENP), J1.A4 (VBUS), J1.A9 (VBUS), J1.B4 (VBUS), J1.B9 (VBUS), R51.1, TP11.1
/USB-C_PhonePC/CC1: C46.1, C89.1, J4.A5 (CC1), TP15.1, U11.A3 (CC1)
/USB-C_PhonePC/CC2: C45.1, C95.1, J4.B5 (CC2), TP29.1, U11.A4 (CC2)
/USB-C_PhonePC/D+: J4.A6 (Dp1), J4.B6 (Dp2), R32.1, TP14.1, U15.3 (IO2)
/USB-C_PhonePC/D-: J4.A7 (Dn1), J4.B7 (Dn2), R33.1, TP13.1, U15.2 (IO1)
/USB-C_PhonePC/SBU1: J4.A8 (SBU1), R38.2
/USB-C_PhonePC/SBU2: J4.B8 (SBU2), R40.2
/USB-C_PhonePC/VBUS: C96.1, C97.1, D3.1 (K), J4.A4 (VBUS), J4.A9 (VBUS), J4.B4 (VBUS), J4.B9 (VBUS), JP4.1 (A), TP30.1
/USB-PD-PhonePC/DN1: TP16.1, U11.E1 (DN1)
/USB-PD-PhonePC/DP2: TP17.1, U11.E2 (DP2)
/USB-PD-PhonePC/GPIO0: IC1.B3 (EN), R37.2, R38.1, U11.E6 (GPIO0)
/USB-PD-PhonePC/GPIO1: R39.2, R40.1, R65.2, U11.B4 (GPIO1)
/USB-PD-PhonePC/GPIO3: R37.1, R39.1, U11.D5 (GPIO3)
/USB-PD-PhonePC/VIO1: JP1.2 (B), JP6.2 (B)
/USB-PD-PhonePC/VIO1_: C54.1, JP6.1 (A), R36.1, TP22.1, U11.B1 (VIO1)
/USB-PD-PhonePC/VIO2_: C53.1, JP5.1 (A), R34.1, R35.1, TP21.1, U11.C1 (VIO2)
/VBoost: C32.2, C33.2, C34.2, C40.1, C41.1, C42.1, C43.1, OUT1.1, U6.D4 (OUT), U6.E1 (FB), U6.E4 (OUT), U6.E5 (OUT), U6.E6 (OUT), U8.4 (VCC), U9.4 (VCC), U9.7 (A0)
GND: BT1.2 (-), C1.2, C2.2, C3.2, C4.2, C5.2, C6.2, C7.2, C8.2, C9.2, C10.2, C11.2, C12.2, C13.2, C14.2, C15.2, C16.2, C17.2, C18.2, C19.2, C20.2, C21.2, C22.2, C23.2, C24.2, C25.2, C26.2, C27.2, C28.2, C29.1, C32.1, C33.1, C34.1, C35.2, C36.2, C37.2, C38.2, C39.2, C40.2, C41.2, C42.2, C43.2, C44.2, C45.2, C46.2, C47.2, C48.2, C49.2, C50.2, C51.2, C52.2, C53.2, C54.2, C55.2, C57.2, C58.2, C64.2, C66.2, C67.2, C68.2, C69.2, C70.2, C71.2, C72.2, C74.2, C75.2, C76.2, C77.2, C78.2, C80.2, C85.2, C86.2, C87.2, C88.2, C89.2, C90.2, C91.2, C92.2, C93.2, C94.2, C95.2, C96.2, C97.2, C98.2, C99.2, C100.2, C101.2, C102.2, C103.2, C104.2, C105.2, D1.3 (COMMON_ANODE), D2.2 (A), D3.2 (A), D4.1 (K), D5.2 (A), IC1.C1 (GND), IC1.C2 (GND), IC2.3 (GND), IC2.25 (EP), J1.25 (SHLD), J1.A1 (GND), J1.A12 (GND), J1.B1 (GND), J1.B12 (GND), J2.2, J3.5, J3.6, J4.A1 (GND), J4.A12 (GND), J4.B1 (GND), J4.B12 (GND), PGND1.1, Q1.2 (S), R17.2, R26.2, R27.2, R29.2, R30.2, R52.2, R53.2, R54.2, R55.2, R59.1, R60.1, R61.1, R62.2, R63.2, R64.2, TP26.1, TP28.2, U1.2 (GND), U2.4 (GND), U3.19 (TESTEN), U3.57 (GND), U4.B1 (GND), U4.B2 (GND), U4.B3 (GND), U4.C1 (MODE), U4.C2 (GND), U4.C3 (GND), U4.D1 (CRTL), U5.1 (GND), U6.C3 (PGND), U6.C4 (PGND), U6.C5 (PGND), U6.C6 (PGND), U6.C7 (PGND), U6.D1 (SEL), U6.D2 (PGND), U6.D3 (PGND), U6.E2 (AGND), U7.1 (1~OE), U7.4 (2~OE), U7.7 (GND), U7.10 (3~OE), U7.13 (4~OE), U8.5 (GND), U8.7 (A0), U8.8 (A1), U8.11 (GND), U9.5 (GND), U9.8 (A1), U9.11 (GND), U10.7 (GND), U11.C5 (GND_A), U11.D4 (GPIO6_I2C_ADDR), U11.D6 (GND_D), U12.B2 (NC), U12.D1 (VSS), U13.2 (THM), U13.4 (BATSN), U13.13 (DGND), U13.14 (PGND), U13.15 (PGND), U13.16 (PGND), U13.28 (AGND), U14.B2 (RSET_LDO), U14.B4 (GND), U14.B5 (GND), U14.C1 (ENLDO), U14.E2 (GND), U14.E5 (PGND), U15.1 (GND), U16.C1 (GND)
unnamed: BT1.1 (+), C59.2, C61.1, R41.1, R42.1, R43.2, R44.2
unnamed: BT1.3, C55.1, C56.1, U12.E1 (REG25)
unnamed: BT1.4, C56.2, U12.E2 (TS)
unnamed: C3.1, R5.2, Y1.2
unnamed: C6.1, C7.1, C8.1, U3.23 (DVDD), U3.45 (VREG_VOUT), U3.50 (DVDD)
unnamed: C28.1, U6.C1 (VL)
unnamed: C30.1, U6.A3 (BST1)
unnamed: C30.2, L1.1, U6.A7 (LX1), U6.B5 (LX1), U6.B6 (LX1), U6.B7 (LX1)
unnamed: C31.1, L1.2, U6.D5 (LX2), U6.D6 (LX2), U6.D7 (LX2), U6.E7 (LX2)
unnamed: C31.2, U6.E3 (BST2)
unnamed: C47.1, JP2.2 (B), U11.A5 (VCIN)
unnamed: C48.1, JP3.2 (B), U11.B6 (SYS)
unnamed: C49.1, U11.C6 (AVL)
unnamed: C50.1, JP4.2 (B), U11.A6 (VBUS), U16.A1 (VOUT), U16.B1 (VOUT)
unnamed: C51.1, U11.A2 (VDD1P1)
unnamed: C52.1, U11.B5 (VDD1P8)
unnamed: C57.1, R42.2, U12.C2 (BAT)
unnamed: C58.1, R41.2, U12.C1 (VPWR)
unnamed: C59.1, C60.1, R43.1, U12.B1 (SRN)
unnamed: C60.2, C61.2, R45.1, U12.A1 (SRP)
unnamed: C62.1, Q2.1 (SOURCE1), Q2.3 (SOURCE1), R44.1, R45.2
unnamed: C62.2, C63.1
unnamed: C64.1, R48.2, U12.B3 (PACKP)
unnamed: C65.2, C66.1
unnamed: C71.1, JP7.2 (B), R49.1, U13.27 (VIO)
unnamed: C72.1, U13.3 (VDD)
unnamed: C73.1, U13.20 (BST)
unnamed: C73.2, L2.1, U13.17 (LX), U13.18 (LX), U13.19 (LX)
unnamed: C77.1, C80.1, D7.1 (Cathode), U13.21 (BYP)
unnamed: C84.1, L3.1, U14.C4 (LXB), U14.D4 (LXB)
unnamed: C84.2, U14.D5 (BST)
unnamed: C88.1, U14.A4 (LDO)
unnamed: C98.1, C99.1, C100.1, IC1.A1 (VOUT), IC1.A2 (VOUT), U16.A2 (VIN), U16.B2 (VIN)
unnamed: C102.1, IC2.12 (V3VD)
unnamed: C103.1, IC2.20 (V5V)
unnamed: C104.1, IC2.15 (IFB)
unnamed: D1.1 (1_CATHODE), R8.2, R10.2, R12.1
unnamed: D1.2 (2_CATHODE), R9.2, R11.2, R13.1
unnamed: D4.2 (A), R57.2
unnamed: D6.1 (K), R56.1
unnamed: IC1.B1 (SW), IC1.B2 (SW), L4.2
unnamed: IC2.6 (GPIO4), R57.1
unnamed: IC2.7 (VSEL1), R59.2
unnamed: IC2.9 (VSEL0), R60.2
unnamed: IC2.11 (VSEL2), R61.2
unnamed: IC2.13 (PSEL), R62.1
unnamed: IC2.23 (PWR_EN), R58.2
unnamed: IC2.24 (VCC), Q3.3 (D), R51.2
unnamed: JP8.2 (B), U13.31 (SUSPND)
unnamed: JP9.2 (B), U13.1 (DISQBAT)
unnamed: L3.2, U14.E4 (LXA)
unnamed: Q2.2 (GATE1), R46.1
unnamed: Q2.5 (GATE2), R47.1
unnamed: Q3.1 (G), Q4.1 (G), R58.1, R66.2
unnamed: Q3.2 (S), Q4.2 (S), R66.1
unnamed: R3.2, U3.47 (USB_DP)
unnamed: R4.2, U3.46 (USB_DM)
unnamed: R12.2, TP5.1
unnamed: R13.2, TP6.1
unnamed: R16.1, U4.B4 (VINA_S)
unnamed: R19.2, U5.8 (EN)
unnamed: R20.2, SDA1V1.1, U5.4 (A2), U6.B1 (SDA)
unnamed: R21.2, SCL1V1.1, U5.3 (A1), U6.A1 (SCL)
unnamed: R22.2, U7.11 (4Y)
unnamed: R23.2, U7.8 (3Y)
unnamed: R24.2, U7.6 (2Y)
unnamed: R25.2, U7.3 (1Y)
unnamed: R26.1, R29.1, U8.2 (ISENSE)
unnamed: R27.1, R30.1, U9.2 (ISENSE)
unnamed: R32.2, U11.D1 (DN)
unnamed: R33.2, U11.D2 (DP)
unnamed: R46.2, U12.A2 (CHG)
unnamed: R47.2, U12.A3 (DSG)
unnamed: R50.1, U13.26 (EXTSM)
unnamed: R50.2, TP12.1
unnamed: R52.1, U14.B3 (RSET_SBB0)
unnamed: R53.1, U14.A3 (RSET_SBB1)
unnamed: R54.1, U14.A2 (RSET_SBB2)
unnamed: R55.1, U14.C2 (RSET_IPK)
unnamed: R56.2, U13.29 (STAT)
unnamed: R65.1, U16.C2 (ON)

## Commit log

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2021-07-01 ForkArms v2
    Wider opening to accept puck, 1mm down to accept rec coil being offset from bottom, more material on top to push puck down, and lofted hole to align from many angles
    [ForkArmLeft.stl, ForkArmRight.stl, UM2WOB_pcb-masterPartbase.3mf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]
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2021-07-09 1mm off bottoms of arms and tail to prevent wheels slipping
    [ForkArmLeft.stl, ForkArmRight.stl, MirrorMount.FCStd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]
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2021-10-14 Updated battery mount arms to look smoother and added model for new wireless cahrger slot
    [Robot_Puck-ForkArmRight (Mirror #1).stl, Robot_Puck-robot_assembly_AP203Fillet001.stl, Robot_Puck-robot_assembly_AP203ForkArmRight.stl]
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2021-10-15 Increased width of gap for coil in holder.
    Printing with width reduced by 97per and 96 per on holder and key respectively seems to fit well with UM2 using 1.0mm head and 0.2mm layer height.
    [Robot_Puck-robot_assembly_AP203wirelessHolder.stl, Robot_Puck-robot_assembly_AP203wiressKey.stl]
2021-11-08 prior to printing more pucks for art expo. Made hole in bottom of puck for easier reprogramming
    [pcb.FCStd, puck_base.stl, puck_top.stl]
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2022-04-08 Some overwritten changes by swapping back to robot project
    [ChargerIC.kicad_sch, LDO.kicad_sch, USB-PD.kicad_sch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]
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2022-06-03 Added missing resistors to led paths
    [Top.kicad_sch, USB-PD.kicad_sch]
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2022-06-03 Added missing Vmcu wire and cleaned things up
    [USB-PD.kicad_sch]
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2022-07-27 Added initial battery charger schematic based on typical application circuit and pin descriptions
    [Charger.kicad_sch, Hardware.kicad_sch, Top.kicad_sch]
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2022-08-03 wip started working on pd sheet but need more info before proceeding
    [Top.kicad_sch, USB-PD.kicad_sch]
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2022-08-18 Seperated and added 3V3 to MCU for USB and AVD supply
    As per Sections 2.9.4, 2.9.5 and 2.9.7.3 of the rp2040 datasheet
    [RP2040_minimal.kicad_sch]
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2022-08-19 Added switches for swapping I2C master between MCU and external
    [Hardware.kicad_sch, Top.kicad_sch]
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2022-08-25 replaced all shunt jumpers with better symbols
    [Charger.kicad_sch, Top.kicad_sch, USB-PD.kicad_sch]
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2022-09-01 Revert "Seperated and added 3V3 to MCU for USB and AVD supply"
    This reverts commit dff833df8ca7cc74c4733d65dcaa8f38f7d04b29.
    [RP2040_minimal.kicad_sch]
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2022-09-01 Fixed net errors on I2C lines for MAX77958 slave and switch
    [Top.kicad_sch]
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2022-09-02 Reworked GPIO pin numbering
    [RP2040_minimal.kicad_sch, robot.kicad_sch]
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2022-09-02 Replaced standard op amp with SN74
    [RP2040_minimal.kicad_sch, robot.kicad_sch]
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2022-09-05 Replaced protection chip with bq27742
    [Protection.kicad_sch]
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2022-09-05 replaced ESD diodes with AZ23C5V6-7-F
    [Protection.kicad_sch, robot.kicad_sch]
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2022-09-09 Colored and reworked I2C buses for clarity
    [robot.kicad_sch]
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2022-09-15 Changed pull-up resistors for MCU I2C Master and External I2C to 1KOhm.
    [robot.kicad_sch]
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2022-09-27 Removed EN_LSF Added 100nF to boost reg and extensive rework to boost sheet
    [RP2040_minimal.kicad_sch, boostRegulator.kicad_sch, robot.kicad_sch]
2022-09-27 Fixed labeling problem in power-mux among cosmetic changes to top sheet
    [powerMux.kicad_sch, robot.kicad_sch]
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2022-09-28 Changed sheet pin from VINA_S to USB_V and corrected memo from 1.8V to 3.3V
    [powerMux.kicad_sch, robot.kicad_sch]
2022-09-28 Added description to nmos and fixed format of net label on top sheet
    [powerMux.kicad_sch, robot.kicad_sch]
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2022-09-28 Removed 1V8 input to MCU as no longer used
    [robot.kicad_sch]
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2022-09-29 Added momentary push switch for MCU reset
    [RP2040_minimal.kicad_sch, robot.kicad_sch]
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2022-09-29 Moved pins back after Updated MAX77976 symbol to remove duplicate power output pin types
    [Charger.kicad_sch]
2022-09-29 Removed shorts on PD I2C sheet pins
    [robot.kicad_sch]
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2022-09-29 Updated power input to power output on LX and BST pins for MAX77857 and removed previously assigned power flags
    [boostRegulator.kicad_sch, robot.kicad_sch]
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2022-09-30 Added DNP to thermistor as I will need to manually install it with the battery cell
    [Protection.kicad_sch, robot.kicad_sch]
2022-09-30 Fixed typo in thermistor
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2022-09-30 Changed values of Motor{1,2} to DRV8830DRCR and added text replacing motor # refs
    [motors.kicad_sch, robot.kicad_sch]
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2022-10-03 Correct RSET resistance for 3V3 and 1V8 pins on simo
    [LDO.kicad_sch, robot.kicad_sch]
2022-10-03 Revert "Correct RSET resistance for 3V3 and 1V8 pins on simo"
    This reverts commit 3c014a89efb1627164809f39dad8e492ec139191.
    [LDO.kicad_sch, robot.kicad_sch]
2022-10-03 Updated RESET_IPK to 14k to allow higher current limits and <100% inductor utilization from xls sheet
    [LDO.kicad_sch, robot.kicad_sch]
2022-10-03 Copied boost inductor over to simo as they need similar specs and can save on part count.
    [LDO.kicad_sch, robot.kicad_sch]
2022-10-03 Added missing annotations
    [LDO.kicad_sch, robot.kicad_sch, usb-c.kicad_sch]
2022-10-04 Updated spdt reset switch to two pads to be shorted via external wire
    [RP2040_minimal.kicad_sch, robot.kicad_sch]
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2022-10-04 Replaced charger diode with one used in USB-C
    [Charger.kicad_sch, robot.kicad_sch]
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2022-10-04 replaced TVS diodes on DP/DN lines
    [USB-PD.kicad_sch, robot.kicad_sch]
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2022-10-04 Replaced push switch with 2-pad shorting TP
    [Charger.kicad_sch, robot.kicad_sch]
2022-10-04 Replaced footprint with 2 pad short test point
    [RP2040_minimal.kicad_sch, robot.kicad_sch]
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2022-10-05 Added part and footprint for mux mosfet.
    Swapped pins 2 and 3 to match part.
    [powerMux.kicad_sch, robot.kicad_sch]
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2022-10-06 Correct error on pin location
2022-10-06 MAJOR REVISION. MAX77958 moved to new sheet and 2nd USB connector added
    [USB-PD-ExtChg.kicad_sch, USB-PD-PhonePC.kicad_sch, robot.kicad_sch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]
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2022-10-07 Cosmetic rework of USB-PD-PhonePC
    [USB-PD-PhonePC.kicad_sch]
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2022-10-12 Replaced common drain dual mosfet with two single ones
    [USB-PD-ExtChg.kicad_sch, robot.kicad_sch]
2022-10-12 Replaced dual mosfet with cheaper pair and common source.
    [USB-PD-PhonePC.kicad_sch, robot.kicad_sch]
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2022-10-17 Replaced switch with cheaper jumpers and adds ability to add to circuit externally if necessary for debugging
    [USB-PD-PhonePC.kicad_sch, robot.kicad_sch]
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2022-10-17 Changed net names to resolve duplicate nets
    [USB-PD-PhonePC.kicad_sch]
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2022-10-17 fixed overlapping silkscreen
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2022-10-19 Reverting some of the offset vias I made since VIP seems unavoidable on the 0.4mm pitch parts
2022-10-20 decreased tolerances down to 0.1mm and moved a few things to meet this
2022-10-20 Added a few more 0.1mm tolerances
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2022-10-20 Marked DNP parts as out of BOM and added some fab instructions
    [Protection.kicad_sch]
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2022-10-20 Apparently didn't save the GND pad properties before
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2022-11-15 removed footprint based vias as triggering annuallar ring DRC error. Kadir please add more if think they are necessary
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2022-11-17 Mainly just small value resistor tweaks and notes on their required power ratings.
    [Protection.kicad_sch, USB-PD-ExtChg.kicad_sch, motors.kicad_sch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]
2022-11-18 bulk BOM edits. Mainly dealing with cap voltage ratings and part selection
    [Charger.kicad_sch, LDO.kicad_sch, Protection.kicad_sch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]
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2022-11-18 Replaced DNP 1210 caps with onboard 0603 DNP caps on backside
    [Charger.kicad_sch, robot.kicad_sch]
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2022-11-24 Moved usb-c-phonepc into USB-PD-PhonePC and fixed inverted dn/dp pins
    [USB-PD-PhonePC.kicad_sch, robot.kicad_sch, usb-c-phonepc.kicad_sch]
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2022-11-28 Swapped out ESD diodes on I2C lines
    [robot.kicad_sch]
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2022-11-28 Swapped out ESD diodes on DN/DP lines
    [USB-PD-PhonePC.kicad_sch]
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2022-11-28 Fixed remaining ERC errors
    [RP2040_minimal.kicad_sch, USB-PD-ExtChg.kicad_sch, USB-PD-PhonePC.kicad_sch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]
2022-11-28 Fixed incorrect wiring of ESD on I2C lines
    [robot.kicad_sch]
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2022-11-28 Bulk BOM edits and one replaced footprint for U15
    [Charger.kicad_sch, LDO.kicad_sch, Protection.kicad_sch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]
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2022-12-09 Parts number swap on U17. Just reel size
    [USB-PD-PhonePC.kicad_sch, robot.kicad_sch]
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2023-02-03 replaced R43 and R45 part numbers
    [Protection.kicad_sch]
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2023-03-08 wip replacement of r57 and D4:
    [USB-PD-ExtChg.kicad_sch, robot.kicad_sch]
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2023-06-05 Swapped sda and scl on USB-PD-PhonePC to correct past mistake
    [robot.kicad_sch]
2023-06-05 Swapping GPIO16 to GPIO8 to free up UART0
    [RP2040_minimal.kicad_sch, robot.kicad_sch]
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2023-07-19 Add button for boot select like on PICO to allow drag/drop programming
    [RP2040_minimal.kicad_sch]
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2023-07-19 Add test points for testing current on SIMO. Also add shunt switches to turn on/off each (i.e. on pins D2, D1, and E1).
    [LDO.kicad_sch]
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2023-07-19 custom_transistors:ON_Semiconductor-568AL-10_2013-O-MFG footprint 3d model dot to correct corner
    [Protection.kicad_sch]
2023-07-19 Added set resistor for LDO and changed size to 0603 for LDO output capacitor as recommended by datasheet Output Capacitor Selection
    [LDO.kicad_sch]
2023-07-19 Enable LDO and set it at 1.8V and Disable SBB2 and follow recommendations for unused outputs
    [LDO.kicad_sch]
2023-07-19 Added pull-down resistors between U17 and U16 to prevent floating voltages.
    [USB-PD-PhonePC.kicad_sch]
2023-07-19 Swap out R62 from 45.3k to 16k
    [USB-PD-ExtChg.kicad_sch]
2023-07-19 Swap pins on J3 to match micromotors
    [motors.kicad_sch]
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2023-07-26 Updating kicad_common.json to correct directories
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2023-07-26 Adding switch to connect d+/- from both USB from Pc to pi
    [USB-PD-ExtChg.kicad_sch, USB-PD-PhonePC.kicad_sch, robot.kicad_sch]
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2023-07-26 Flipping battery to other side of board
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2023-07-27 Eleminated 5V rail and corrected a few mistakes in SIMO config
    [LDO.kicad_sch, robot.kicad_sch]
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2023-07-31 STEP to step and fixed wrong reference naming
    [12401610E4#2A.step]
2023-07-31 Fixed S2 footprint reference
    [RP2040_minimal.kicad_sch]
2023-07-31 Fixed floating zone supposed to be GND
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2023-07-31 Exported all schematic symbols to local robot and refer to them in all symbols
    [Charger.kicad_sch, LDO.kicad_sch, Protection.kicad_sch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]
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2023-07-31 Replaced all jumpers with 0 ohm resistors
    [LDO.kicad_sch, USB-PD-PhonePC.kicad_sch, robot.kicad_sch]
2023-07-31 removed i2c switch for external master. Not needed due to not using custom scripts on the Max77958 in favor of mcu control via firmware
    [robot.kicad_sch]
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2023-07-31 Swapping out SW4_PTS815 SJM 250 SMTR LFS_CNK for prevvious tactile switch on rp2040
    [RP2040_minimal.kicad_sch]
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2023-08-01 Replaced all test points with SMD parts where possible
    [Charger.kicad_sch, USB-PD-ExtChg.kicad_sch, USB-PD-PhonePC.kicad_sch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]
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2023-08-01 Adding a few options for pin headers for GPIO unused and UART
    [RP2040_minimal.kicad_sch]
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2023-08-01 Add bypass cap to power outputs on SIMO to get rid of electrical rules error
    [LDO.kicad_sch]
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2023-08-01 Adding THT leads for rocker switch and 2 ohm resistors to implement it if needed
    [Protection.kicad_sch]
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2023-08-02 Swapped all LEDS out for board edge ones
    [Charger.kicad_sch, LDO.kicad_sch, Protection.kicad_sch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]
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2023-08-02 Replacing LEDs with side mounted ones, and added an LED driver for the two that don't have a driver
    [LDO.kicad_sch, Protection.kicad_sch, RP2040_minimal.kicad_sch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]
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2023-08-05 Moving pololu wheels over to local packages and upgraded to 90mm wheels
    [pololu-wheel-70x8mm-white.step]
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2023-08-07 Increased clearance on mounting holes
    [robot.kicad_sch]
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2023-08-08 Replaced wireless charger header with something that can handle 3A
    [Protection.kicad_sch, robot.kicad_sch]
2023-08-08 changing UART header to 2.54mm header and moving bulk capacitance after load switch.
    [Protection.kicad_sch, RP2040_minimal.kicad_sch]
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2023-08-09 GPIO21 swapped to GPIO22 to enable the buffers
    [RP2040_minimal.kicad_sch, robot.kicad_sch]
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2023-08-09 Adding pin numbers for connector to remove PCB error
    [robot.kicad_sch]
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2023-08-09 Permanently resolving some ERC errors related to updates to symbol libraries
    [LDO.kicad_sch, Protection.kicad_sch]
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2023-08-10 updating all footprints from lib. Rotated a bunch of pads from 270 to 90 and so forth. Looks like might have come from when flipped all parts to other side of board?
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2023-08-11 Updated errors in SN74AHC125RGYR footprint including non-mask defined pads
2023-08-11 Moving mounting holes in 1mm each to avoid courtyard conflicts
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2023-08-11 fixed c37-c17 gnd connection error
2023-08-11 c11-c15 gnd connection error
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2023-08-11 Moving keepout to usb footprint so don't get error from usb footprint being there
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2023-08-11 Updating courtyard on battery. 3d model profile was wrong
    [battery_footprint.FCStd]
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2023-08-13 Added all netties and net classes for 3A traces to schematic and updated PCB, but haven' t routed anything yet
    [Charger.kicad_sch, Protection.kicad_sch, powerMux.kicad_sch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]
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2023-08-13 fixing a few more BOM related issues
    [Charger.kicad_sch, LDO.kicad_sch, Protection.kicad_sch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]
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2023-08-14 fixing Charger.kicad_sch net tie needs on STAT LED and EXTSM also needed to be a signal trace
    [Charger.kicad_sch]
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2023-08-14 fixed drc errors for TP12
    [Charger.kicad_sch]
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2023-08-14 fixing DRC errors associated with SYS in for USB-PD-PhonePC sheet
    [USB-PD-PhonePC.kicad_sch, robot.kicad_sch]
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2023-08-14 fixing net tie issue with VBUS_Phone_PS and nearby nets
    [USB-PD-PhonePC.kicad_sch]
2023-08-14 Adding missing trace on R33
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2023-08-15 fixed drc error and warnings
    [Charger.kicad_sch, LDO.kicad_sch, Protection.kicad_sch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]
2023-08-15 BOM value fixes
    [USB-PD-PhonePC.kicad_sch, motors.kicad_sch]
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2023-08-15 Rename sheet pin to USB_Phone_SYS to remove ERC error
    [USB-PD-PhonePC.kicad_sch, robot.kicad_sch]
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2023-08-17 fixing in_bom for several symbols
    [Charger.kicad_sch, boostRegulator.kicad_sch, motors.kicad_sch]
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2023-08-18 Fixing Vcin net tie issue
    [robot.kicad_sch]
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2023-08-18 Resolving reamining ERC warnings/errors
    [USB-PD-ExtChg.kicad_sch]
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2023-08-23 Changed 4.7uF caps to 0603 and update ref names for wireless sheet as caused BOM issues
    [USB-PD-PhonePC.kicad_sch, Wireless-Receiver.kicad_sch, motors.kicad_sch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]
2023-08-23 Updating all wireless passives to required part numbers. Still missing less restrictive ones
    [Wireless-Receiver.kicad_sch]
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2023-08-25 fixed two wrong product foorprint mismatches
    [Wireless-Receiver.kicad_sch]
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2023-09-05 Replacing wrong part number for USB4151-GF-C
    [USB-PD-PhonePC.kicad_sch]
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2023-09-20 Updating drill origin in gerbers for comparison to working gerbers from NextPCB
    [robot-B_Courtyard.gbr, robot-Bottom Layer.gbr, robot-Bottom Overlay.gbr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]
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2023-10-25 Updating hole sizes to 1.7mm diameter and sending full assembly via 3mf file to Mouez.
    [UMS5_robot3.3mf, robot3.stl]
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2023-11-28 Renaming GPIO16 to correct GPIO8 net
    [robot.kicad_sch]
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2024-02-05 Updating size of shaft adapter after initial batch print failed
    [robot3.stl, shaft-adapter.stl]
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2024-07-24 Adjusting fastener lengths, and fixing clearance to tapped holes in some places.
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2024-07-25 Added missing hole for switch
    [UMS5_robot3.3mf]
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2024-07-29 Adding switch mount fix part to model
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2025-05-28 WIP Total rework of model from ground up
    [body.FCStd, electronicAssembly.FCStd, motor.FCStd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]
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2025-10-07 Fixing switch cutout cutout length.
    [body.FCStd]
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

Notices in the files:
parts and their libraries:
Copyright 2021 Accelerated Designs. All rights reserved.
